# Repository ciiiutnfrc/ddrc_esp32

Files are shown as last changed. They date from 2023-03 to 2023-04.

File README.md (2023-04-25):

# DDRC-ESP32: Controlador para robot de tracción diferencial basado en ESP32

DDRC-ESP32 (Differential Driver Robot Controller con ESP32) es una placa de control embebido para robots de tracción diferencial. 
El controlador diferencial está basado en el módulo [ESP32-WROOM-32E](https://www.espressif.com/sites/default/files/documentation/esp32-wroom-32e_esp32-wroom-32ue_datasheet_en.pdf) de la marca [Espressif](https://www.espressif.com/), el cual cuenta con un SoC (System On Chip) modelo [ESP32-D0WD-V3](https://www.espressif.com/sites/default/files/documentation/esp32_datasheet_en.pdf).
La elección de este módulo se debe principalmente a que está soportado por [micro-ROS](https://micro.ros.org/docs/overview/hardware/). 

El desarrollo del controlador diferencial se llevó a cabo como Proyecto Final de la carrera de Ingeniería Electrónica en la [Facultad Regional Córdoba](https://www.frc.utn.edu.ar/) de la Universidad Tecnológica Nacional.
El título del proyecto es _"Controlador Embebido para Robot de Tracción Differencial"_ y fue desarrollado por Gustavo Albarrán, Dante Ruiz y Juan Nicolodi bajo la dirección del Ing. Gonzalo Perez-Paina y del Ing. Diego Gonzalez Dondo.

Este controlador tiene por finalidad servir de base al desarrollo de robots de tracción diferencial cuyos algoritmos de navegación y control estén basados en [ROS 2](http://docs.ros.org/).

Las funciones principales del controlador diferencial son:
1. Leer la información de los codificadores ópticos acoplados a las ruedas de tracción.
1. Ajustar las velocidades de los motores de tracción mediante controladores PID.
1. Realizar el cálculo de la odometrı́a con la información de los codificadores ópticos acoplados a las ruedas.
1. Leer la tensión de la(s) batería(s) del robot.
1. Comunicarse con la PC a bordo del robot.

La siguiente imagen muestra un render del PCB del controlador diferencial.
<p align="center">
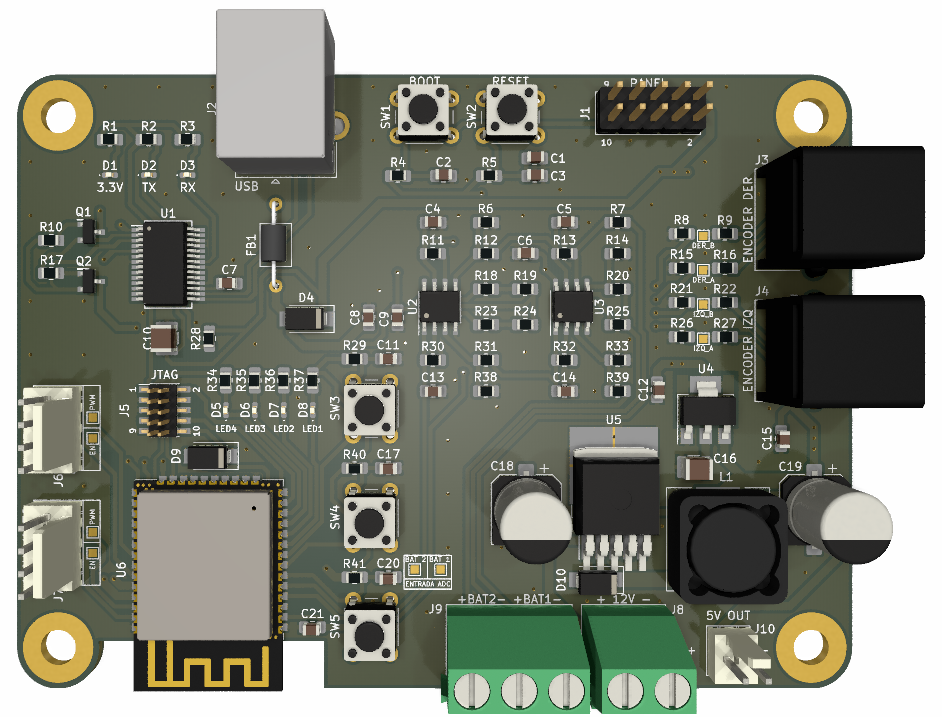
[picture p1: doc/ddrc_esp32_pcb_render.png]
DDRC-ESP32render
  
</p>

## Videos

* [Proyecto Final: Controlador para robot de tracción diferencial compatible con ROS 2](https://www.youtube.com/watch?v=9FsznQ60jsQ&ab_channel=CIIIUTN-FRC)

## Documentación adicional

* [Ejemplo `blink` con ESP-IDF y Docker](doc/IDFBlinkDocker.md)
* [Nodo micro-ROS de ejemplo en ESP32 con Docker](doc/ESP32MicroROS.md).
* [Servidor HTTP para evaluación sobre un robot móvil](doc/HTTPServerDDR.md).

## Licencia
  <p xmlns:cc="http://creativecommons.org/ns#" xmlns:dct="http://purl.org/dc/terms/"><a property="dct:title" rel="cc:attributionURL" href="https://github.com/ciiiutnfrc/ddrc_esp32">DDRC-ESP32: Controlador para robot de tracción diferencial basado en ESP32</a> by <span property="cc:attributionName">Gustavo Albarran, Dante Ruiz, Juan Nicolodi, Diego Gonzalez Dondo, Gonzalo Perez Paina</span> is licensed under <a href="http://creativecommons.org/licenses/by-sa/4.0/?ref=chooser-v1" target="_blank" rel="license noopener noreferrer" style="display:inline-block;">CC BY-SA 4.0</a></p>

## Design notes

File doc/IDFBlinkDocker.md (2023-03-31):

# Ejemplo `blink` con ESP-IDF y Docker

El framework de desarrollo oficial de Espressif se llama [ESP-IDF](https://docs.espressif.com/projects/esp-idf/en/latest/esp32/) (IoT Development Framework).
Para utilizar este framework es necesario instalar las siguientes herramientas:
1. El toolchain para compilar el código fuente del ESP32.
1. Las herramientas de construcción (como CMake y Ninja) para crear aplicaciones con el ESP32.
1. El propio ESP-IDF que contiene la API (bibliotecas de software y código fuente) para el ESP32 junto a varios scripts para operar con el toolchain.

Espressif brinda una [imagen Docker](https://docs.espressif.com/projects/esp-idf/en/latest/esp32/api-guides/tools/idf-docker-image.html) con el IDF listo para usar.
A continuación se muestran los pasos para instalar ESP-IDF usando Docker.

## Instalación de imagen Docker

La imagen se puede buscar con el siguiente comando:
```
> docker search espressif/idf
NAME                          DESCRIPTION                                     STARS     OFFICIAL   AUTOMATED
espressif/idf                 https://docs.espressif.com/projects/esp-idf/…   43                   
espressif/idf-rust-examples   Examples of rust on esp32                       2                    
espressif/idf-rust            ESP-IDF image with Rust support for Xtensa b…   7
```

Luego, la instalación de la imagen se realiza con:
```
> docker pull espressif/idf
```

La imágen instalada es:
```
 > docker images
espressif/idf                 latest             c82768a177c2   14 hours ago    4.16GB
```

El contenedor se puede ejecutar con el siguiente comando:
```
> docker run --rm -v $PWD:/home/esp-idf -w /home/esp-idf -it espressif/idf
```

El ESP-IDF incluye la herramienta de línea de comandos [`idf.py`](https://docs.espressif.com/projects/esp-idf/en/latest/esp32/api-guides/tools/idf-py.html) que sirve de front-end para administrar y construir los proyectos de forma simple. 
Se puede ver la instalada con:
```
> idf.py  --version

ESP-IDF v5.1-dev-3710-gacac972f70
```

## Ejemplo `blink`

Para la construcción y grabación del ejemplo `blink` primero ejecutar el contendor:
```
> docker run --rm --device=/dev/ttyUSB0:/dev/ttyUSB0 -it espressif/idf
```

El ejemplo `blink` se encuentra en `/opt/esp/idf/examples/get-started/blink/`.

Ir al directorio del ejemplo y seguir los siguientes pasos (basados en [enlace](https://github.com/espressif/esp-idf/tree/master/examples/get-started/blink)):
  1. Ingresar a la configuración del proyecto con `idf.py menuconfig`
  1. Ir a `Example Configuration`
  1. Modificar el GPIO del LED (en el controlador diferencial el `LED1` se encuentra en el `GPIO33`)
  1. Salir y guardar los cambios
  1. Construir con `idf.py build`
  1. Grabar con `idf.py -p /dev/ttyUSB0 flash`

El `LED1` de la placa comienza a parpadear cada 1 seg.

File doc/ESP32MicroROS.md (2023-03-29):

# Nodo micro-ROS ejemplo en ESP32 con Docker

Se muestran los pasos a seguir para construir y grabar en la placa un nodo ejemplo de micro-ROS utilizando Docker.

La información de esta página se obtuvo de los siguientes enlaces:
* [micro-ROS setup (github)](https://github.com/micro-ROS/micro_ros_setup)
* [micro-ROS porting to ESP32](https://micro.ros.org/blog/2020/08/27/esp32/)

## ROS 2 en Docker

Ejecutar un contenedor Docker a partir de la imagen de ROS 2 (`ros:galactic-desktop`):
```
> mkdir $HOME/ros2_ws && cd $HOME/ros2_ws
> docker run -it -v $PWD:/home/ros2_ws -w /home/ros2_ws --net=host --privileged --name micro_ros_esp32 --device=/dev/ttyUSB0:/dev/ttyUSB0 osrf/ros:galactic-desktop
```

Actualizar el SO e instalar PIP:
```
> apt update
> apt install vim python3-pip
```

## micro-ROS para ESP32
Crear el espacio de trabajo para ROS 2 con soporta al ESP32, instalar las dependencias y construirlo:
```
> git clone -b $ROS_DISTRO https://github.com/micro-ROS/micro_ros_setup.git src/micro_ros_setup
> rosdep update && rosdep install --from-paths src --ignore-src -y
> colcon build
> source install/local_setup.bash
```

Crear el entorno de trabajo para el firmware del ESP32:
```
> ros2 run micro_ros_setup create_firmware_ws.sh freertos esp32
```

Configurar el proyecto del ESP32 a utilizar:
```
> ros2 run micro_ros_setup configure_firmware.sh int32_publisher -t udp -i [your local machine IP] -p 8888
> ros2 run micro_ros_setup build_firmware.sh menuconfig
```

Utilizar el menú para configuración del proyecto para configurar la conexión WiFi. 
Ir a la opción `micro-ROS Transport Settings` luego `WiFi Connection` y escribir el nombre (`WiFi SSID`) y la clave (`WiFi Password`) de la conexión de red a utilizar.

Construir el proyecto:
```
> ros2 run micro_ros_setup build_firmware.sh
```

Descargar el programa en el microcontrolador:
```
> ros2 run micro_ros_setup flash_firmware.sh
```

## Ejecución del agente y prueba del nodo

Descargar, construir y ejecutar el agente:
```
> ros2 run micro_ros_setup create_agent_ws.sh
> ros2 run micro_ros_setup build_agent.sh
> source install/local_setup.bash
> ros2 run micro_ros_agent micro_ros_agent udp4 --port 8888
```

Abrir otra terminal del contenedor en ejecución:
```
> docker exec -it micro_ros_esp32 bash
```

y ver la información de nodos y tópicos:
```
> source /opt/ros/galactic/setup.bash
> ros2 node list
/freertos_int32_publisher

> ros2 topic list
/freertos_int32_publisher
/parameter_events
/rosout
```

Mostrar el mensaje enviado por el ESP32:
```
> ros2 topic echo /freertos_int32_publisher
data: 4
- - -
data: 5
- - -
data: 6
```

### Agente desde Docker

También se puede utilizar el agente en un contenedor Docker:
```
> docker run -it --rm --net=host microros/micro-ros-agent:galactic udp4 --port 8888 -v6
```

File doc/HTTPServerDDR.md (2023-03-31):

# Servidor HTTP para evaluación sobre un robot móvil

Esta aplicación sirve para evaluar las funcionalidades del controlador montado sobre un robot de traccióń diferencial. Fue evaluado sobre el Robot móvil [RoMAA-II](https://ciii.frc.utn.edu.ar/wiki/Robotica/RoMAARobot).

Para grabar la aplicación en el controlador se debe clonar el presente repositorio y desde la shell de Linux ir al subdirectorio `src/http_server/`. Una vez en este directorio y con el controlador conectado a la PC, ejecutar:
```
> docker run --rm --device=/dev/ttyUSB0:/dev/ttyUSB0 -v $PWD:/home/http_server -w /home/http_server -it espressif/idf
```

Construir y grabar la aplicación con:
```
> idf.py build
> idf.py flash
```

La aplicación generar una red WiFi con los siguientes datos:
* SSID: ddrc
* Pass: ddrc1234

Una vez conectado a esta red, utilizar un navegador para ingresar a la dirección 192.168.4.1.

Los parámetros de la red (SSID y Pass) se puede modificar utilizando el comando `idf.py menuconfig`.

Para depurar el comportamiento de la aplicación se puede utilizar el monitor del ESP32 con:
```
> idf.py monitor
```

Para salir del monitor utilizar la combinación de teclas `Ctrl+]`.

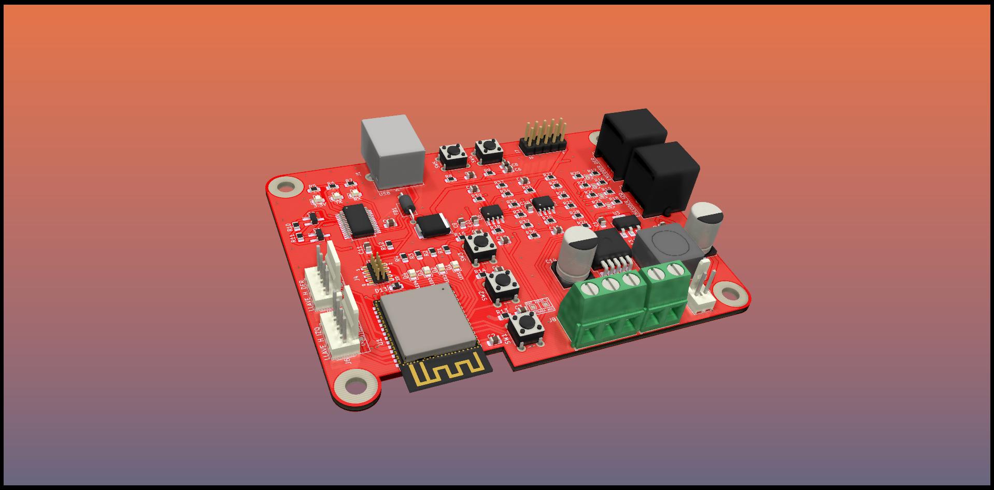
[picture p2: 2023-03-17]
hardware/main_board/imagen_esp_controller_PCB.jpg

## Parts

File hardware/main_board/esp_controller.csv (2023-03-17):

Id | Identificador | Empaquetado | Cantidad | Identificación | Suministrador y ref
1 | TP10,TP8,TP9,TP7,TP6,TP4,TP3,TP5,TP2,TP1 | TestPoint_Pad_1.0x1.0mm | 10 | TP
2 | C21,C20,C19,C18,C17,C16,C12,C10,C8,C7,C6,C5,C4,C3,C2 | C_0805_2012Metric_Pad1.18x1.45mm_HandSolder | 15 | 100nF
3 | U1 | ESP32-WROOM-32E-with-keep-area | 1 | ESP32-WROOM-32E
4 | J10 | Molex_KK-254_AE-6410-02A_1x02_P2.54mm_Vertical | 1 | Conn_01x02
5 | J9 | TerminalBlock_Phoenix_MKDS-1,5-2-5.08_1x02_P5.08mm_Horizontal | 1 | Conn_01x02
6 | D8 | D_SMA_Handsoldering | 1 | 1N5824
7 | J1 | USB_B_OST_USB-B1HSxx_Horizontal | 1 | USB_B
8 | J3,J2 | RJ14_Connfly_DS1133-S4_Horizontal | 2 | RJ14
9 | U6,U5 | SOIC-8_3.9x4.9mm_P1.27mm | 2 | MCP6002-xSN
10 | U4 | TO-263-5_TabPin3 | 1 | LM2596S-5
11 | R39,R38,R12 | R_0805_2012Metric_Pad1.20x1.40mm_HandSolder | 3 | 1k
12 | R37,R36,R27,R26,R25,R24,R23,R22,R21,R20,R15,R14,R13,R11,R10,R9,R8 | R_0805_2012Metric_Pad1.20x1.40mm_HandSolder | 17 | 10k
13 | R35,R33 | R_0805_2012Metric_Pad1.20x1.40mm_HandSolder | 2 | 2.5k
14 | R34,R32 | R_0805_2012Metric_Pad1.20x1.40mm_HandSolder | 2 | 2k
15 | R31,R30,R29,R28 | R_0805_2012Metric_Pad1.20x1.40mm_HandSolder | 4 | 2.2k
16 | R19,R18,R17,R16 | R_0805_2012Metric_Pad1.20x1.40mm_HandSolder | 4 | 27k
17 | R7,R6,R5,R4,R3,R2,R1 | R_0805_2012Metric_Pad1.20x1.40mm_HandSolder | 7 | 270
18 | L1 | L_12x12mm_H8mm | 1 | 33uH
19 | D13 | D_0805_2012Metric_Pad1.15x1.40mm_HandSolder | 1 | D
20 | D12 | D_2816_7142Metric_Pad3.20x4.45mm_HandSolder | 1 | SS34
21 | D7,D6,D5,D4,D3,D2,D1 | LED_0805_2012Metric_Pad1.15x1.40mm_HandSolder | 7 | LED
22 | C15,C14 | CP_Elec_8x11.9 | 2 | 680uF
23 | C13,C1 | C_0805_2012Metric_Pad1.18x1.45mm_HandSolder | 2 | 22uF
24 | C11 | C_0805_2012Metric_Pad1.18x1.45mm_HandSolder | 1 | 4.7uF
25 | C9 | C_0805_2012Metric_Pad1.18x1.45mm_HandSolder | 1 | 10nF
26 | Q2,Q1 | SOT-23_Handsoldering | 2 | S8050
27 | U3 | SOT-223-3_TabPin2 | 1 | AMS1117-3.3
28 | J8 | TerminalBlock_Phoenix_MKDS-1,5-3-5.08_1x03_P5.08mm_Horizontal | 1 | Conn_01x03
29 | J7 | PinHeader_2x05_P2.54mm_Vertical | 1 | Conn_02x05_Odd_Even
30 | J6,J5 | Molex_KK-254_AE-6410-04A_1x04_P2.54mm_Vertical | 2 | Conn_01x04
31 | J4 | PinHeader_2x05_P1.27mm_Vertical_SMD | 1 | Conn_02x05_Odd_Even
32 | SW5,SW4,SW3,SW2,SW1 | SW_PUSH_6mm | 5 | SW_Push
33 | FB1 | L_Axial_L5.0mm_D3.6mm_P10.00mm_Horizontal_Murata_BL01RN1A2A2 | 1 | Ferrite_Bead
34 | U2 | SSOP-28_5.3x10.2mm_P0.65mm | 1 | FT232RL
35 | H4,H3,H2,H1 | MountingHole_4.3mm_M4_Pad | 4 | MountingHole_4.3mm_M4_Pad

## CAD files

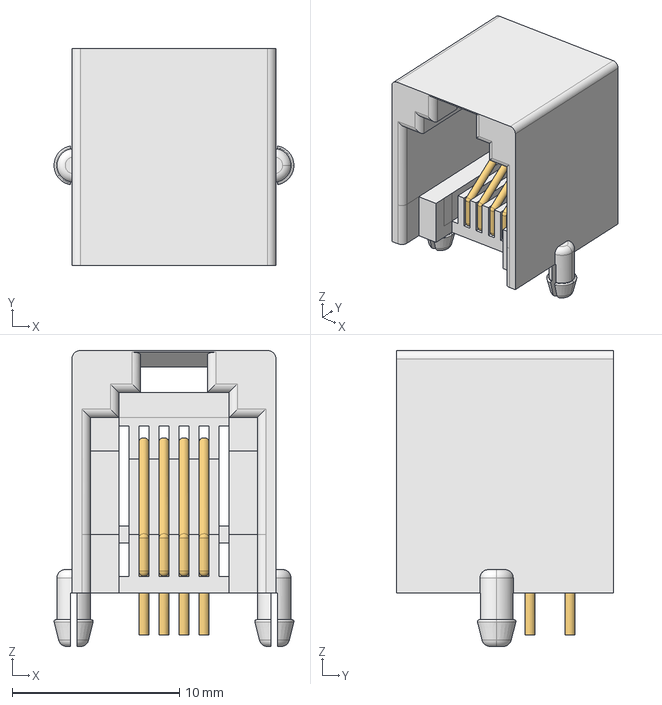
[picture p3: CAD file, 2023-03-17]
hardware/kicad_lib/3d/RJ11.step
14.3 x 13.0 x 17.7 mm

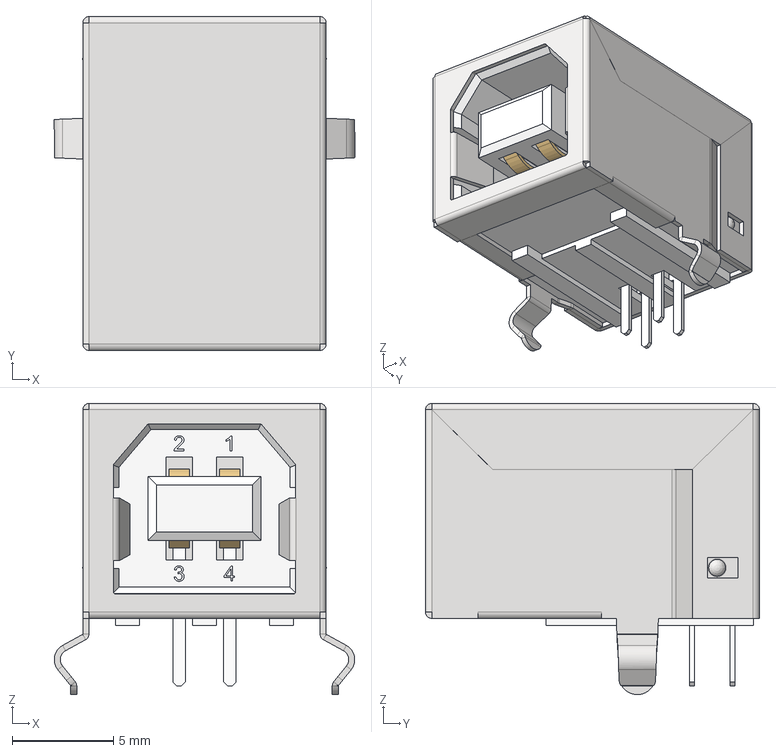
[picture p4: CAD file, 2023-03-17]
hardware/kicad_lib/3d/USB 2.0 Type B Connector Right Angle (Würth 61400416121).stp
14.8 x 16.5 x 14.4 mm

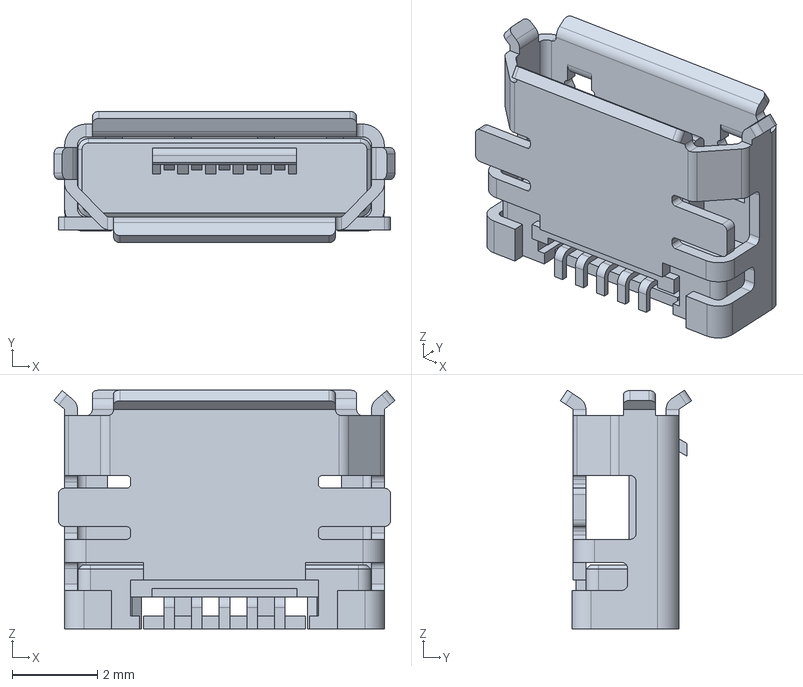
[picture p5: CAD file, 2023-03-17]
hardware/kicad_lib/3d/USB-B-micro.stp
8.00 x 3.08 x 5.60 mm

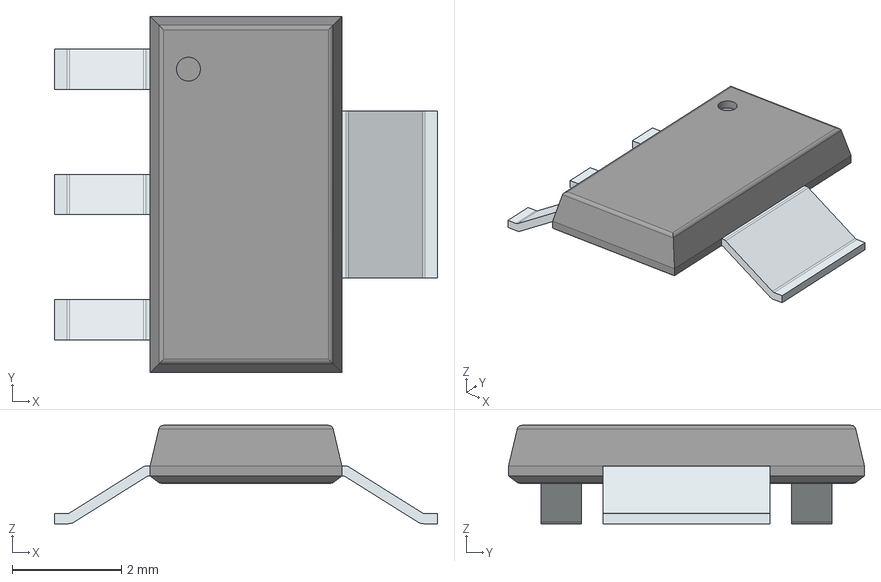
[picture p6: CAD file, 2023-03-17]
hardware/kicad_lib/3d/AMS1117-3.3.stp
7.00 x 6.50 x 1.80 mm
PinsArrayL
FilletPinR

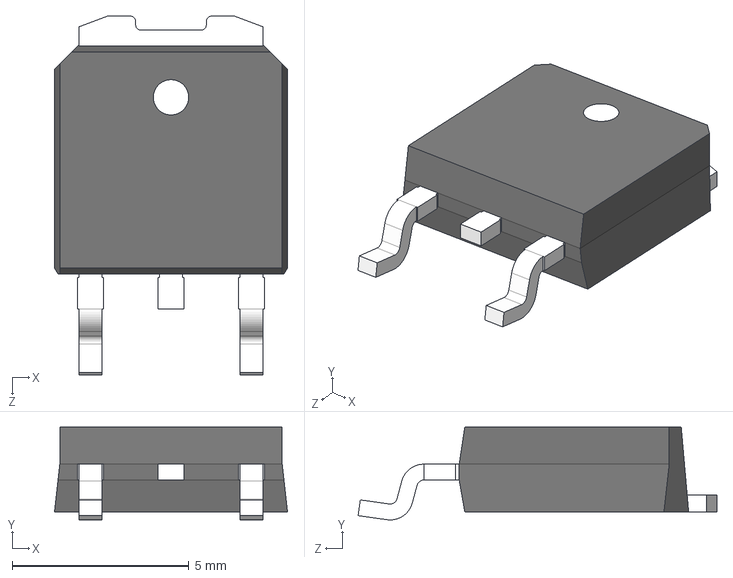
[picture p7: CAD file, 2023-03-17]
hardware/kicad_lib/3d/L7805CDT-TR.stp
6.60 x 2.63 x 10.2 mm

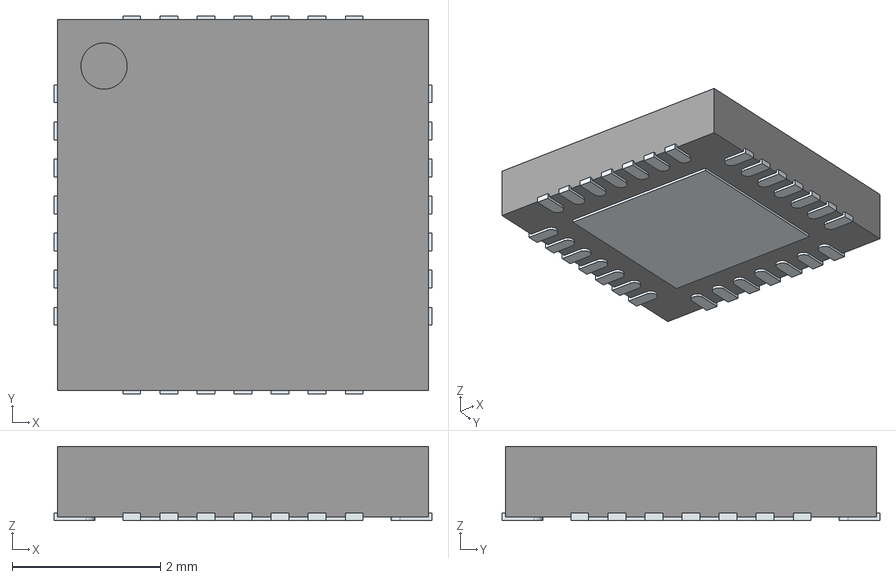
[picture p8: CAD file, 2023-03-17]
hardware/kicad_lib/3d/CP2102-GMR.stp
5.10 x 5.10 x 1.00 mm
ThermalPin
PinsArrayLR
PinsArrayTB

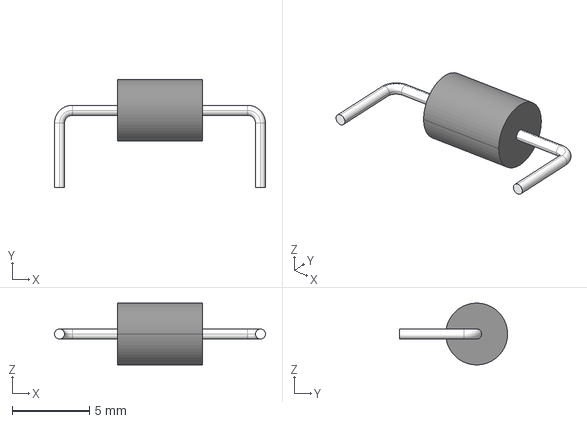
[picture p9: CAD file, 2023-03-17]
hardware/kicad_lib/3d/ferrite-h_p13_d4_l5-5.stp
13.6 x 7.00 x 4.00 mm

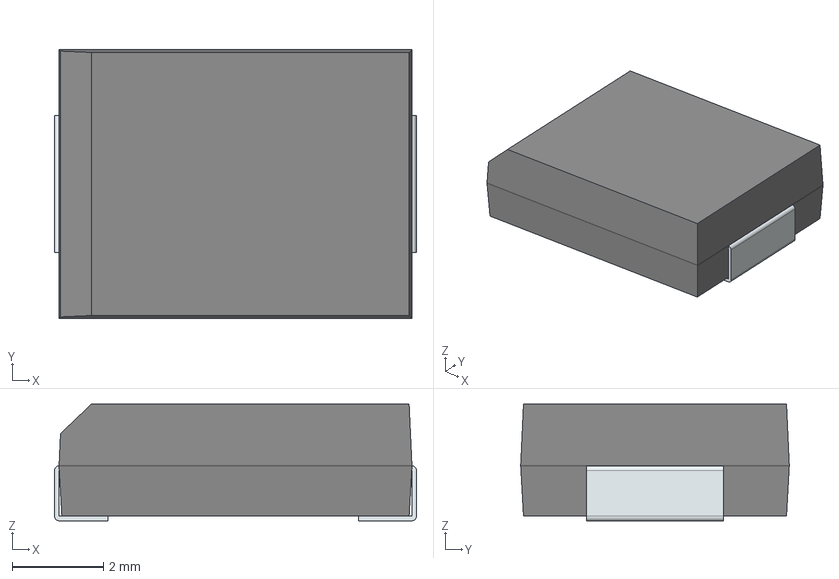
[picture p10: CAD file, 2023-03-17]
hardware/kicad_lib/3d/SS34.stp
7.95 x 5.90 x 2.56 mm
FilletPin1
FilletPin2

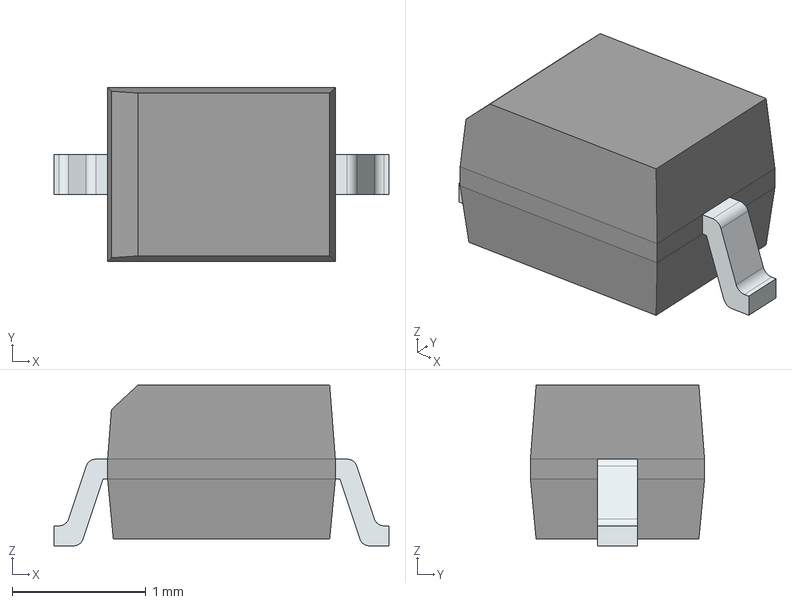
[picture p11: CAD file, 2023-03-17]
hardware/kicad_lib/3d/BAT760-7.stp
2.50 x 1.30 x 1.20 mm
FilletPinL
FilletPinR

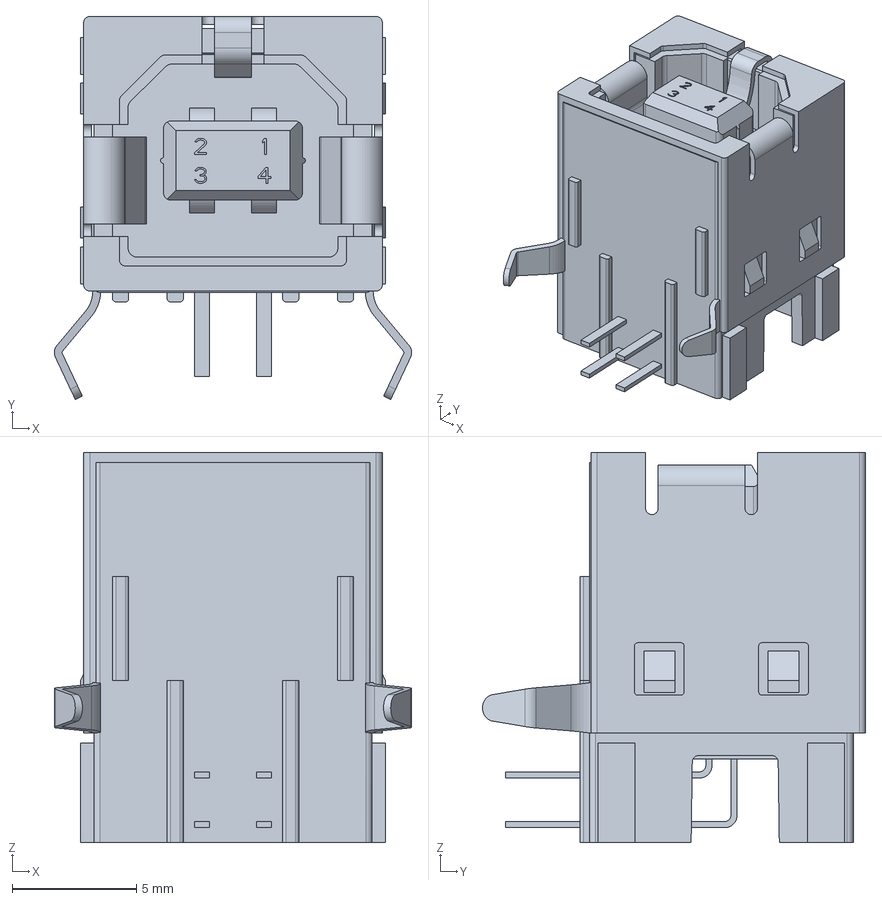
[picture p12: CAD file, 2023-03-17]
hardware/kicad_lib/3d/USB-B.stp
14.4 x 15.4 x 15.7 mm

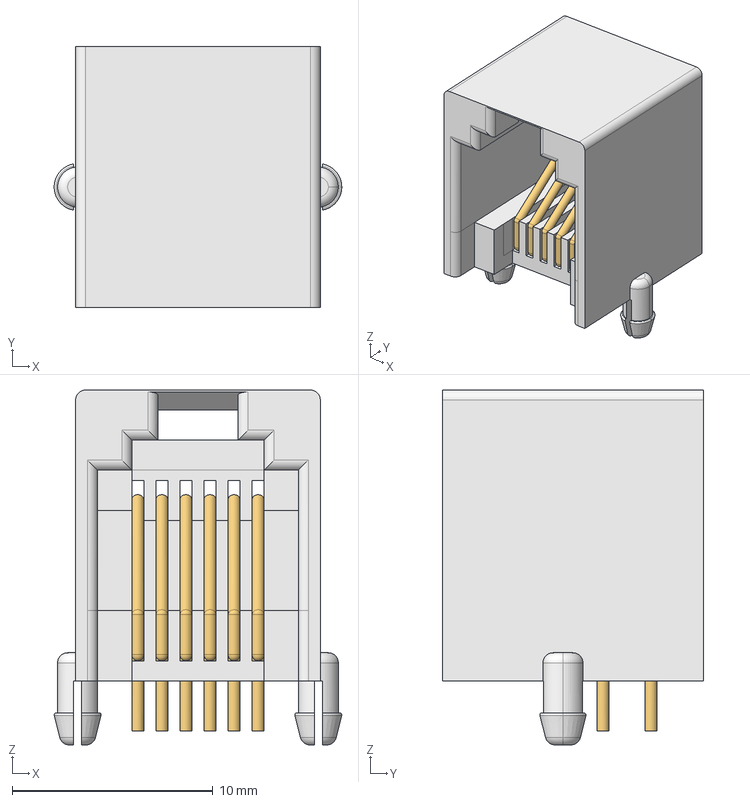
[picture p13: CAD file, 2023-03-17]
hardware/kicad_lib/3d/RJ12.step
14.3 x 13.0 x 17.7 mm

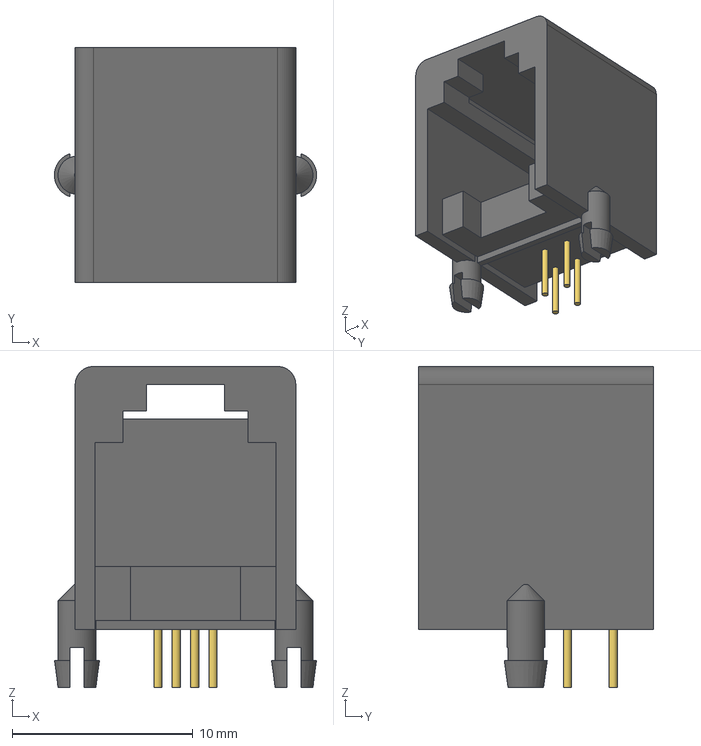
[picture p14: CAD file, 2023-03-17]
hardware/kicad_lib/3d/TJ6P4C.stp
14.5 x 13.0 x 17.8 mm

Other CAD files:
hardware/kicad_lib/3d/BAT760-7.stl
hardware/kicad_lib/3d/SS34.stl

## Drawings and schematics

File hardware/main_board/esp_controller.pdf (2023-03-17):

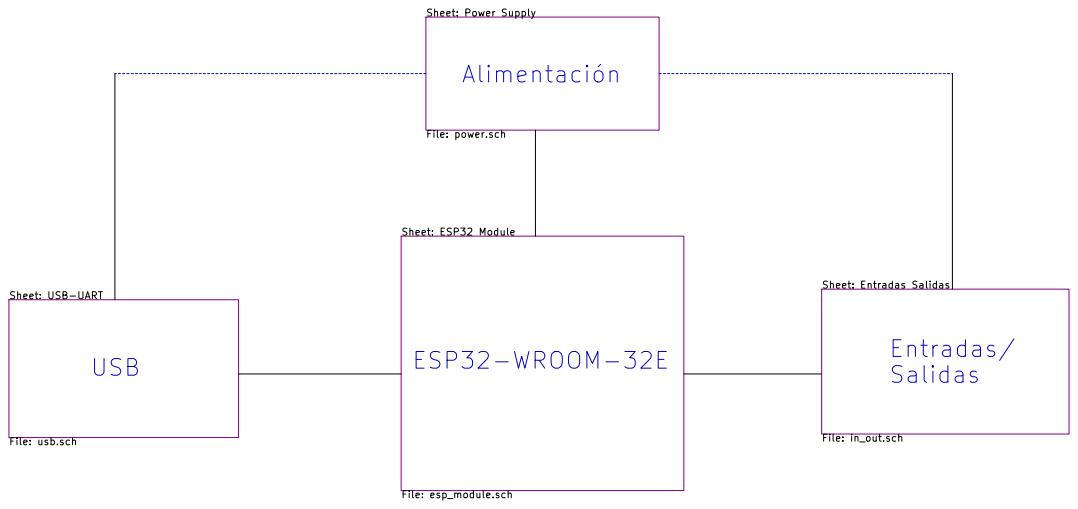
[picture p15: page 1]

Sheet: ESP32 Module File: esp_module.sch Sheet: USB-UART

File: esp_controller.sch Sheet: /
Id: 1/5 Title: Controlador embebido para robot de tracción diferencial

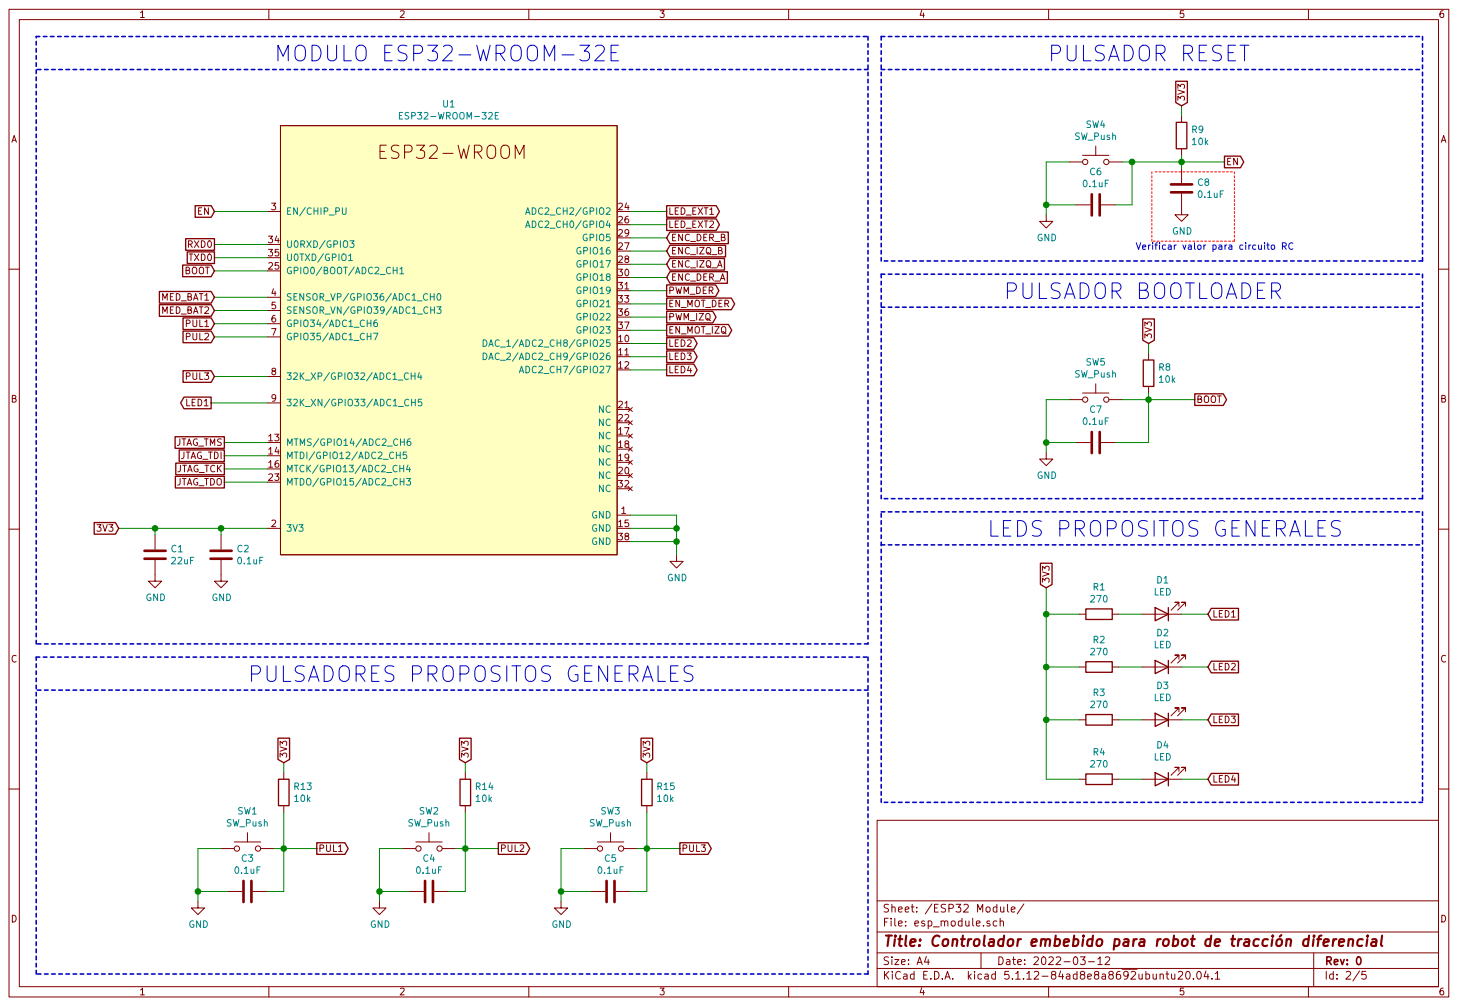
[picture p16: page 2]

Verificar valor para circuito RC

Id: 2/5 Title: Controlador embebido para robot de tracción diferencial

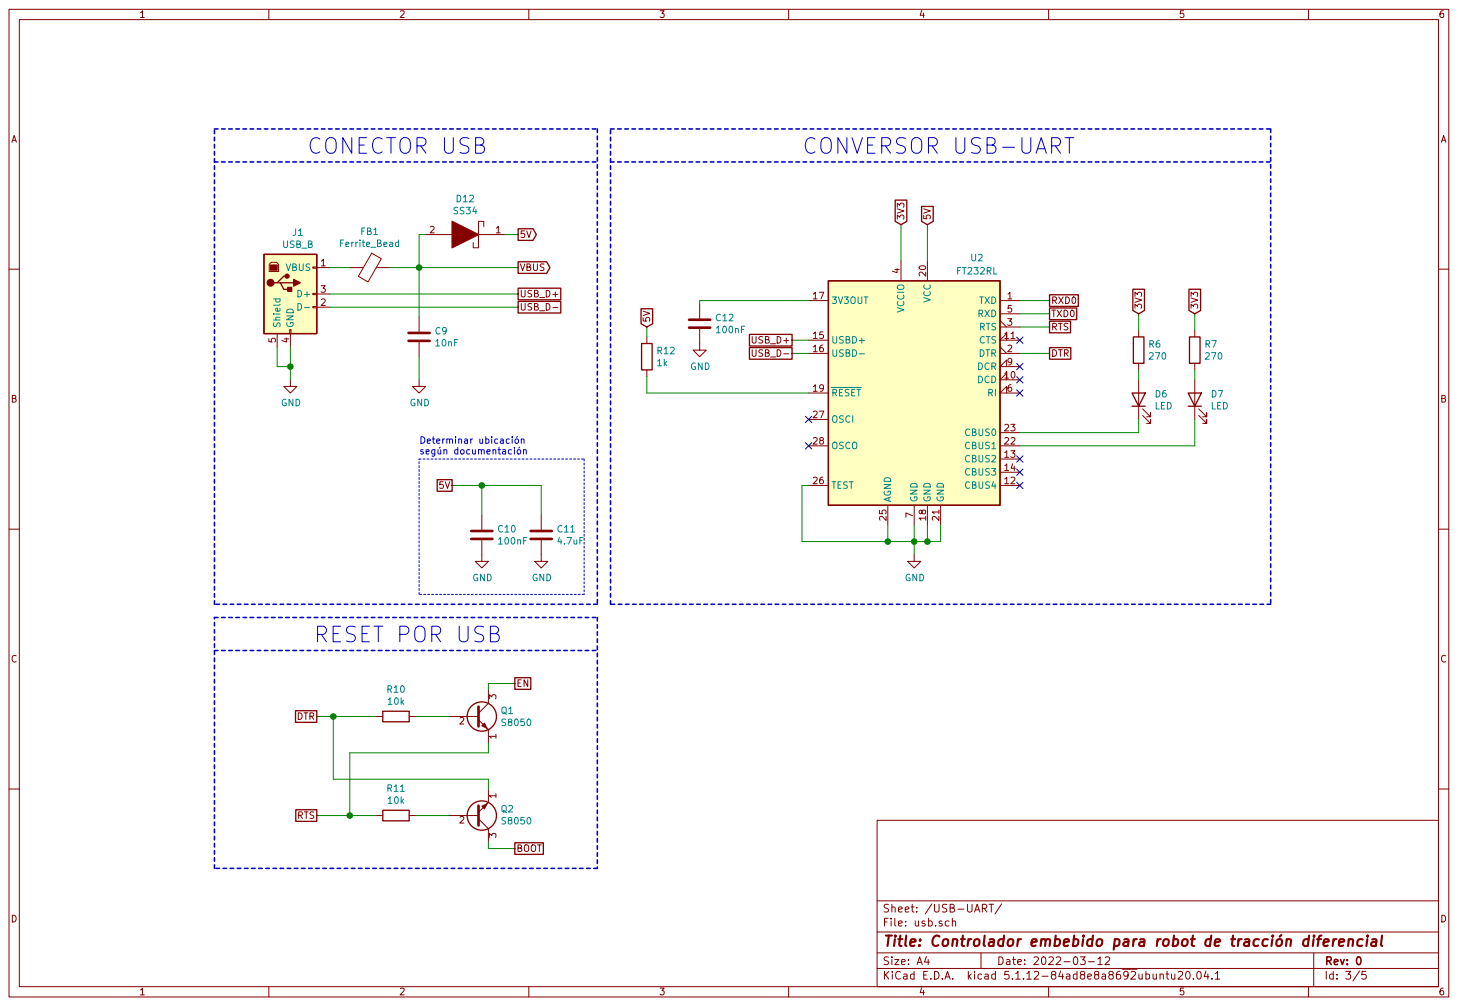
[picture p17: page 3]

Id: 3/5 Title: Controlador embebido para robot de tracción diferencial File: usb.sch Sheet: /USB-UART/ C11

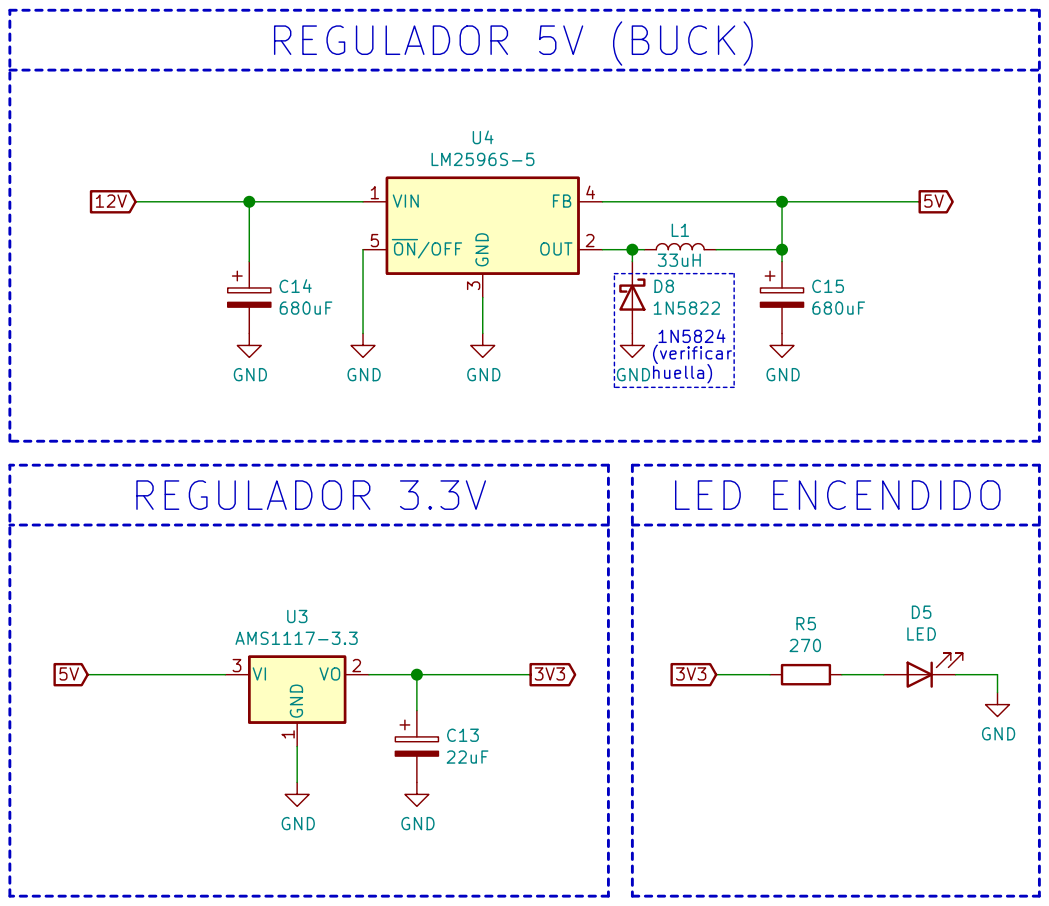
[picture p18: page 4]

File: power.sch
Id: 4/5 Title: Controlador embebido para robot de tracción diferencial

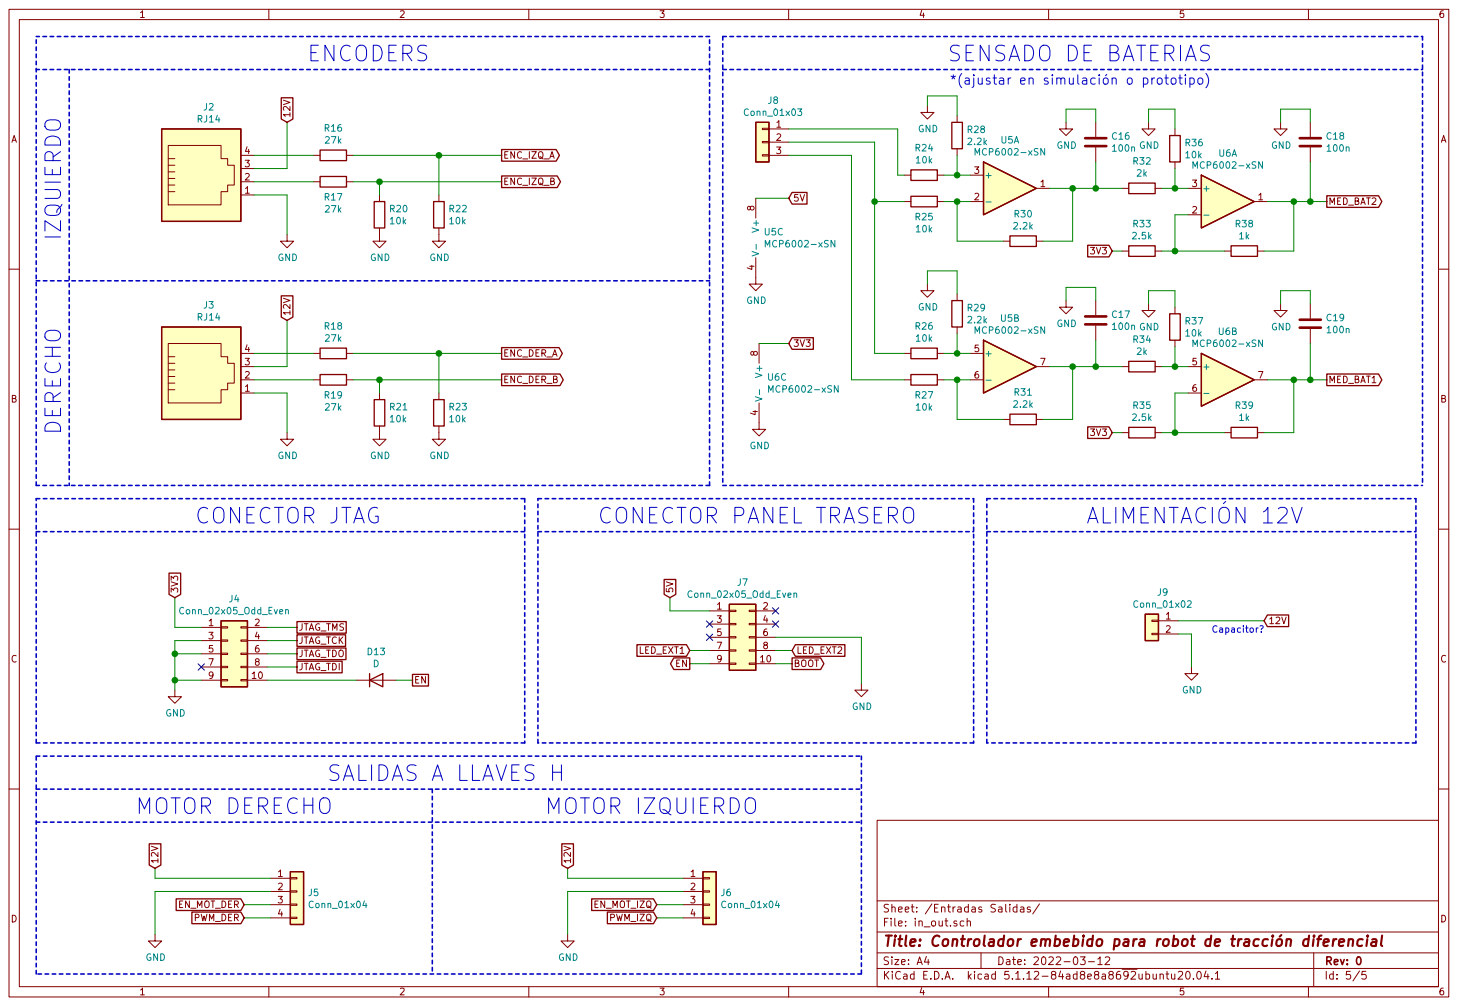
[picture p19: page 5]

*(ajustar en simulación o prototipo) IZQUIERDO

ENC_IZQ_B 12V

10k GND

Id: 5/5 Title: Controlador embebido para robot de tracción diferencial

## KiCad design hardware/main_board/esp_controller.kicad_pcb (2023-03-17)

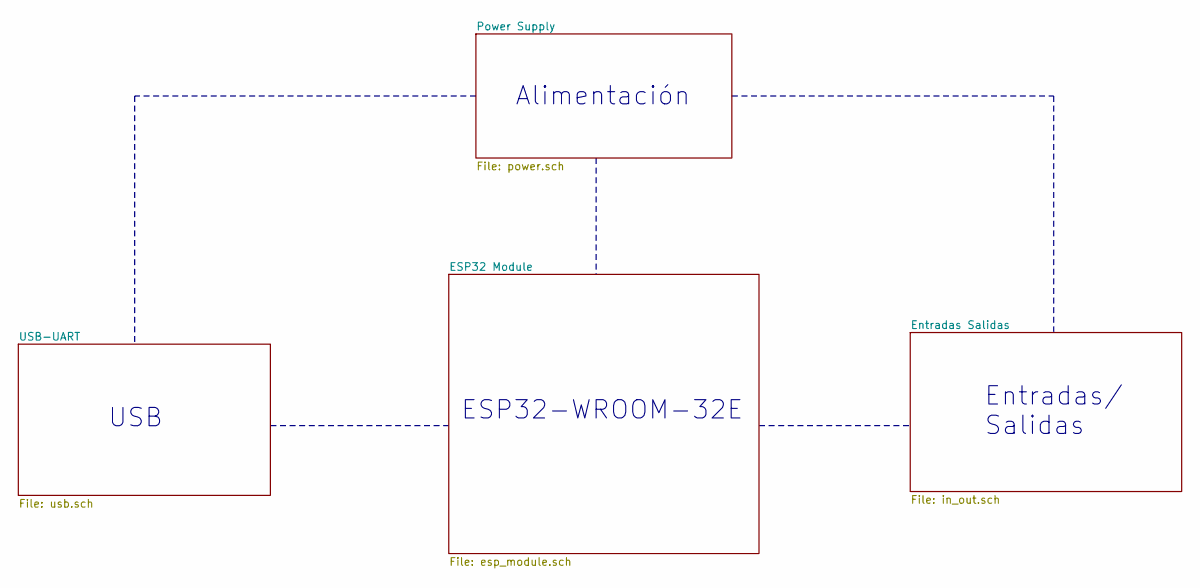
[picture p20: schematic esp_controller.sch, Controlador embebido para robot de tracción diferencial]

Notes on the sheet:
Alimentación
Entradas/ Salidas
USB
ESP32-WROOM-32E

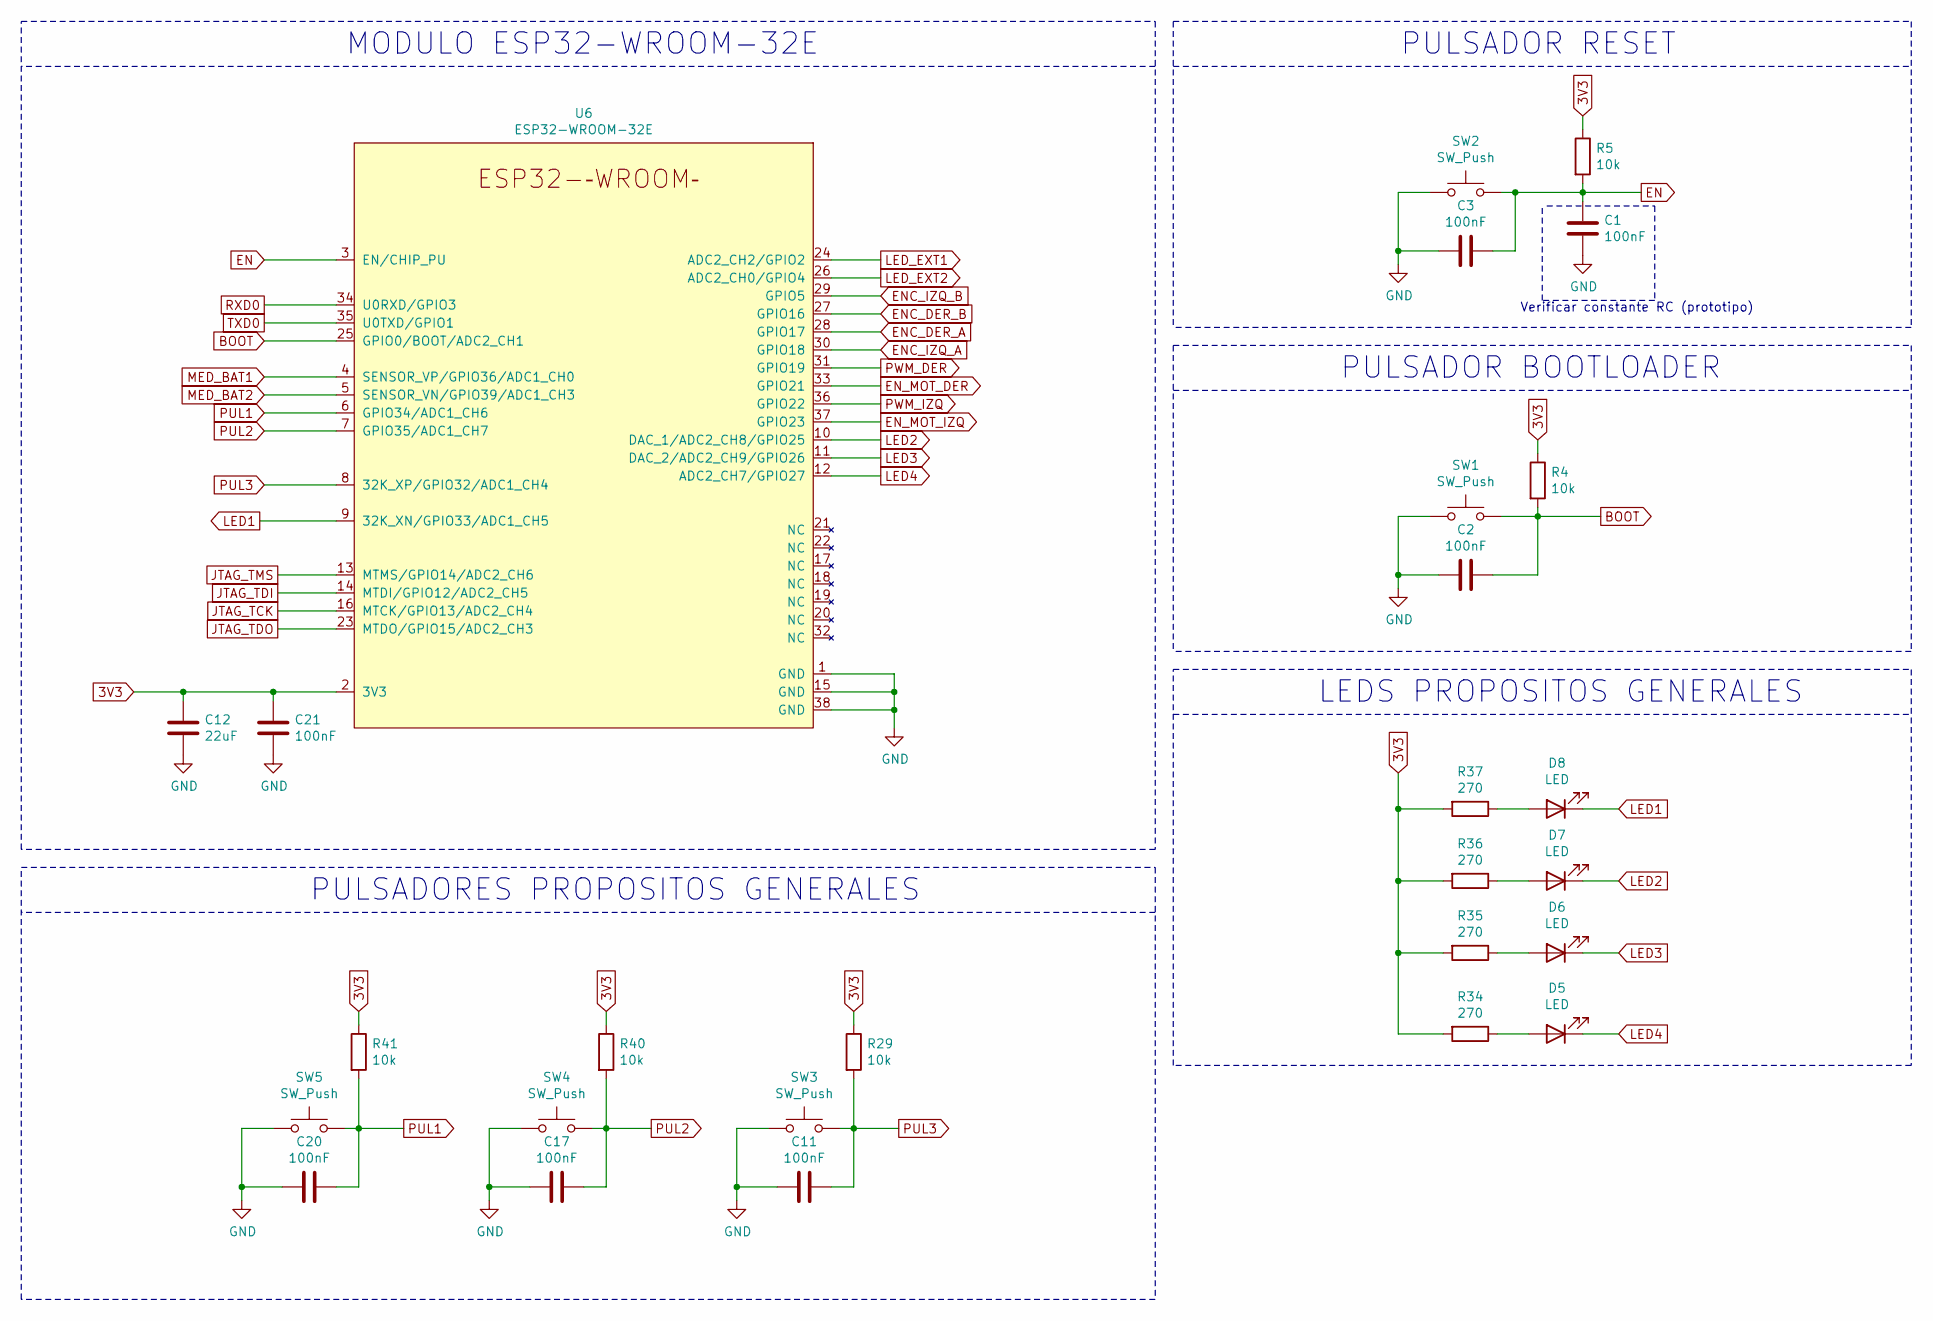
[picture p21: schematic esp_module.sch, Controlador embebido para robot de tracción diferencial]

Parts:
C1, C2, C3, C11, C17, C20, C21: 100nF; C_0805_2012Metric_Pad1.18x1.45mm_HandSolder
C12: 22uF; C_0805_2012Metric_Pad1.18x1.45mm_HandSolder
D5, D6, D7, D8: LED; LED_0402_1005Metric_Pad0.77x0.64mm_HandSolder
R4, R5, R29, R40, R41: 10k; R_0805_2012Metric_Pad1.20x1.40mm_HandSolder
R34, R35, R36, R37: 270; R_0805_2012Metric_Pad1.20x1.40mm_HandSolder
SW1, SW2, SW3, SW4, SW5: SW_Push; SW_PUSH_6mm
U6: ESP32-WROOM-32E; ESP32-WROOM-32E-with-keep-area

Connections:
3V3: C12.1, C21.1, R4.1, R5.1, R29.1, R34.2, R35.2, R36.2, R37.2, R40.1, R41.1, U6.2 (3V3); also elsewhere on the board
BOOT: C2.1, R4.2, SW1.2, U6.25 (GPIO0/BOOT/ADC2_CH1); also elsewhere on the board
EN: C1.1, C3.1, R5.2, SW2.2, U6.3 (EN/CHIP_PU); also elsewhere on the board
ENC_DER_A: U6.28 (GPIO17); also elsewhere on the board
ENC_DER_B: U6.27 (GPIO16); also elsewhere on the board
ENC_IZQ_A: U6.30 (GPIO18); also elsewhere on the board
ENC_IZQ_B: U6.29 (GPIO5); also elsewhere on the board
EN_MOT_DER: U6.33 (GPIO21); also elsewhere on the board
EN_MOT_IZQ: U6.37 (GPIO23); also elsewhere on the board
GND: C1.2, C2.2, C3.2, C11.2, C12.2, C17.2, C20.2, C21.2, SW1.1, SW2.1, SW3.1, SW4.1, SW5.1, U6.1 (GND), U6.15 (GND), U6.38 (GND); also elsewhere on the board
JTAG_TCK: U6.16 (MTCK/GPIO13/ADC2_CH4); also elsewhere on the board
JTAG_TDI: U6.14 (MTDI/GPIO12/ADC2_CH5); also elsewhere on the board
JTAG_TDO: U6.23 (MTDO/GPIO15/ADC2_CH3); also elsewhere on the board
JTAG_TMS: U6.13 (MTMS/GPIO14/ADC2_CH6); also elsewhere on the board
LED1: D8.1 (K), U6.9 (32K_XN/GPIO33/ADC1_CH5)
LED2: D7.1 (K), U6.10 (DAC_1/ADC2_CH8/GPIO25)
LED3: D6.1 (K), U6.11 (DAC_2/ADC2_CH9/GPIO26)
LED4: D5.1 (K), U6.12 (ADC2_CH7/GPIO27)
LED_EXT1: U6.24 (ADC2_CH2/GPIO2); also elsewhere on the board
LED_EXT2: U6.26 (ADC2_CH0/GPIO4); also elsewhere on the board
MED_BAT1: U6.4 (SENSOR_VP/GPIO36/ADC1_CH0); also elsewhere on the board
MED_BAT2: U6.5 (SENSOR_VN/GPIO39/ADC1_CH3); also elsewhere on the board
unnamed: D5.2 (A), R34.1
unnamed: D6.2 (A), R35.1
unnamed: D7.2 (A), R36.1
unnamed: D8.2 (A), R37.1
PUL1: C20.1, R41.2, SW5.2, U6.6 (GPIO34/ADC1_CH6)
PUL2: C17.1, R40.2, SW4.2, U6.7 (GPIO35/ADC1_CH7)
PUL3: C11.1, R29.2, SW3.2, U6.8 (32K_XP/GPIO32/ADC1_CH4)
PWM_DER: U6.31 (GPIO19); also elsewhere on the board
PWM_IZQ: U6.36 (GPIO22); also elsewhere on the board
RXD0: U6.34 (U0RXD/GPIO3); also elsewhere on the board
TXD0: U6.35 (U0TXD/GPIO1); also elsewhere on the board

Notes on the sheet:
PULSADOR RESET
PULSADOR BOOTLOADER
LEDS PROPOSITOS GENERALES
PULSADORES PROPOSITOS GENERALES
MODULO ESP32-WROOM-32E
Verificar constante RC (prototipo)

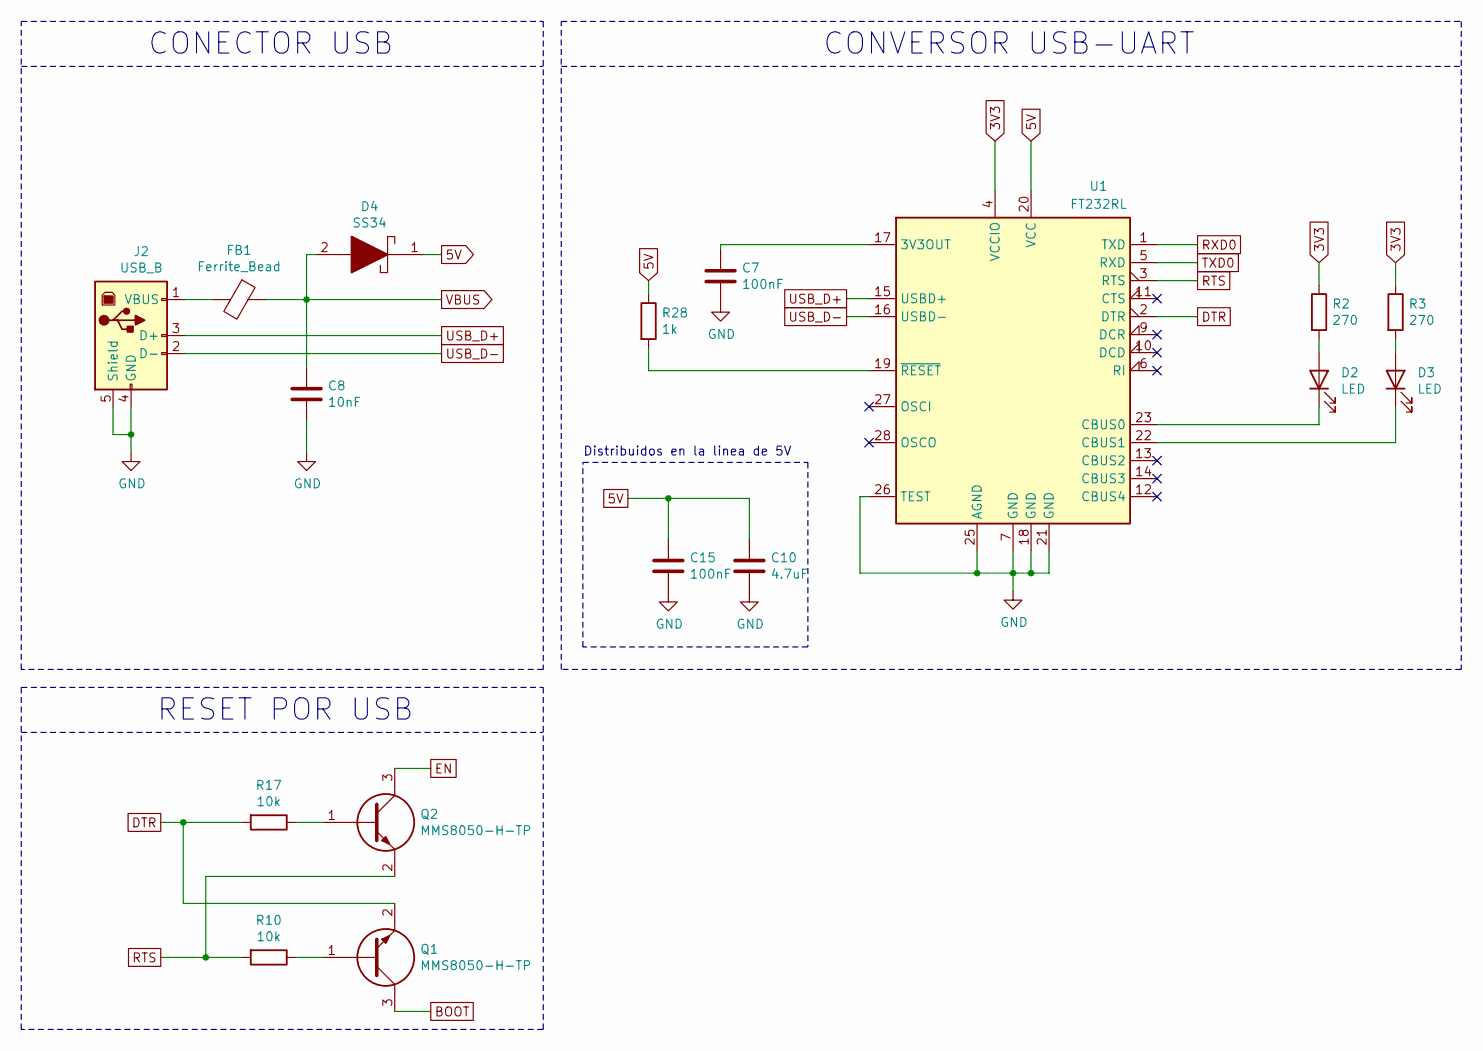
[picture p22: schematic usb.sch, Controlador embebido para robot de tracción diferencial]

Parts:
C7, C15: 100nF; C_0805_2012Metric_Pad1.18x1.45mm_HandSolder
C8: 10nF; C_0805_2012Metric_Pad1.18x1.45mm_HandSolder
C10: 4.7uF; C_1210_3225Metric
D2, D3: LED; LED_0402_1005Metric_Pad0.77x0.64mm_HandSolder
D4: SS34; D_SMA; Manufacturer_Part_Number SS34; Mouser Part Number 512-SS34
FB1: Ferrite_Bead; L_Axial_L5.0mm_D3.6mm_P10.00mm_Horizontal_Murata_BL01RN1A2A2
J2: USB_B; USB_B_OST_USB-B1HSxx_Horizontal
Q1, Q2: MMS8050-H-TP; SOT96P237X122-3N; Manufacturer_Part_Number MMS8050-H-TP; Mouser Part Number 833-MMS8050-H-TP
R2, R3: 270; R_0805_2012Metric_Pad1.20x1.40mm_HandSolder
R10, R17: 10k; R_0805_2012Metric_Pad1.20x1.40mm_HandSolder
R28: 1k; R_0805_2012Metric_Pad1.20x1.40mm_HandSolder
U1: FT232RL; SSOP-28_5.3x10.2mm_P0.65mm

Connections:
3V3: R2.1, R3.1, U1.4 (VCCIO); also elsewhere on the board
5V: C10.1, C15.1, D4.1, R28.1, U1.20 (VCC); also elsewhere on the board
BOOT: Q1.3; also elsewhere on the board
DTR: Q1.2, R17.2, U1.2 (DTR)
EN: Q2.3; also elsewhere on the board
GND: C7.2, C8.2, C10.2, C15.2, J2.4 (GND), J2.5 (Shield), U1.7 (GND), U1.18 (GND), U1.21 (GND), U1.25 (AGND), U1.26 (TEST); also elsewhere on the board
unnamed: C7.1, U1.17 (3V3OUT)
unnamed: D2.1 (K), U1.23 (CBUS0)
unnamed: D2.2 (A), R2.2
unnamed: D3.1 (K), U1.22 (CBUS1)
unnamed: D3.2 (A), R3.2
unnamed: FB1.2, J2.1 (VBUS)
unnamed: Q1.1, R10.1
unnamed: Q2.1, R17.1
unnamed: R28.2, U1.19 (~RESET~)
RTS: Q2.2, R10.2, U1.3 (RTS)
RXD0: U1.1 (TXD); also elsewhere on the board
TXD0: U1.5 (RXD); also elsewhere on the board
USB_D+: J2.3 (D+), U1.15 (USBD+)
USB_D-: J2.2 (D-), U1.16 (USBD-)
VBUS: C8.1, D4.2, FB1.1

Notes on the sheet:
Distribuidos en la linea de 5V
CONECTOR USB
CONVERSOR USB-UART
RESET POR USB

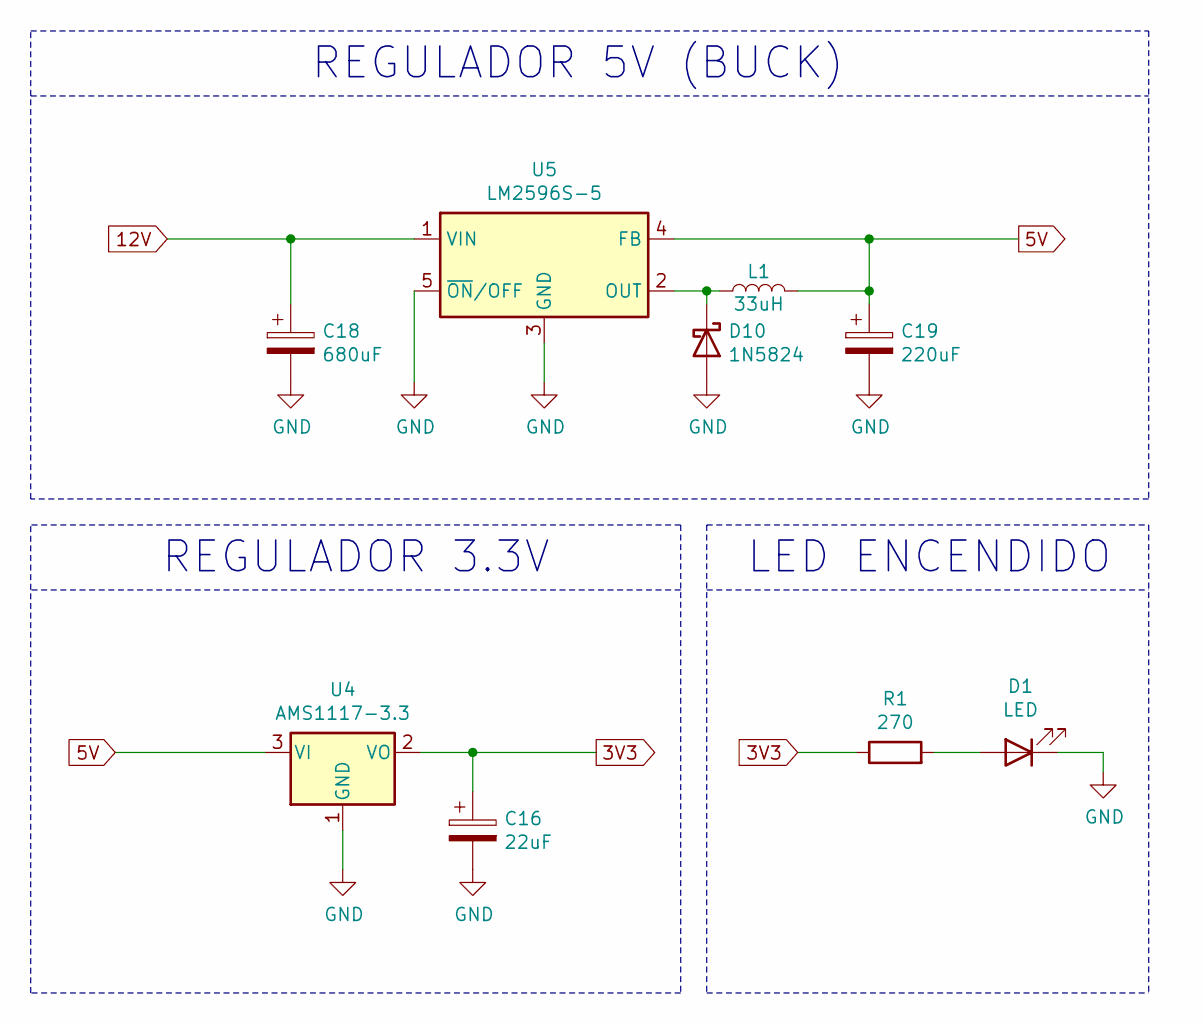
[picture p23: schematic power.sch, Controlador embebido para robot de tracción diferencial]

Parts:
C16: 22uF; C_1210_3225Metric
C18: 680uF; CP_Elec_8x11.9
C19: 220uF; CP_Elec_8x11.9
D1: LED; LED_0402_1005Metric_Pad0.77x0.64mm_HandSolder
D10: 1N5824; D_SMA
L1: 33uH; L_12x12mm_H8mm
R1: 270; R_0805_2012Metric_Pad1.20x1.40mm_HandSolder
U4: AMS1117-3.3; SOT-223-3_TabPin2
U5: LM2596S-5; TO-263-5_TabPin3

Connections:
3V3: C16.1, R1.1, U4.2 (VO); also elsewhere on the board
5V: C19.1, L1.2, U4.3 (VI), U5.4 (FB); also elsewhere on the board
12V: C18.1, U5.1 (VIN); also elsewhere on the board
GND: C16.2, C18.2, C19.2, D1.1 (K), D10.2 (A), U4.1 (GND), U5.3 (GND), U5.5 (~ON~/OFF); also elsewhere on the board
unnamed: D1.2 (A), R1.2
unnamed: D10.1 (K), L1.1, U5.2 (OUT)

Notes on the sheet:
REGULADOR 5V (BUCK)
REGULADOR 3.3V
LED ENCENDIDO

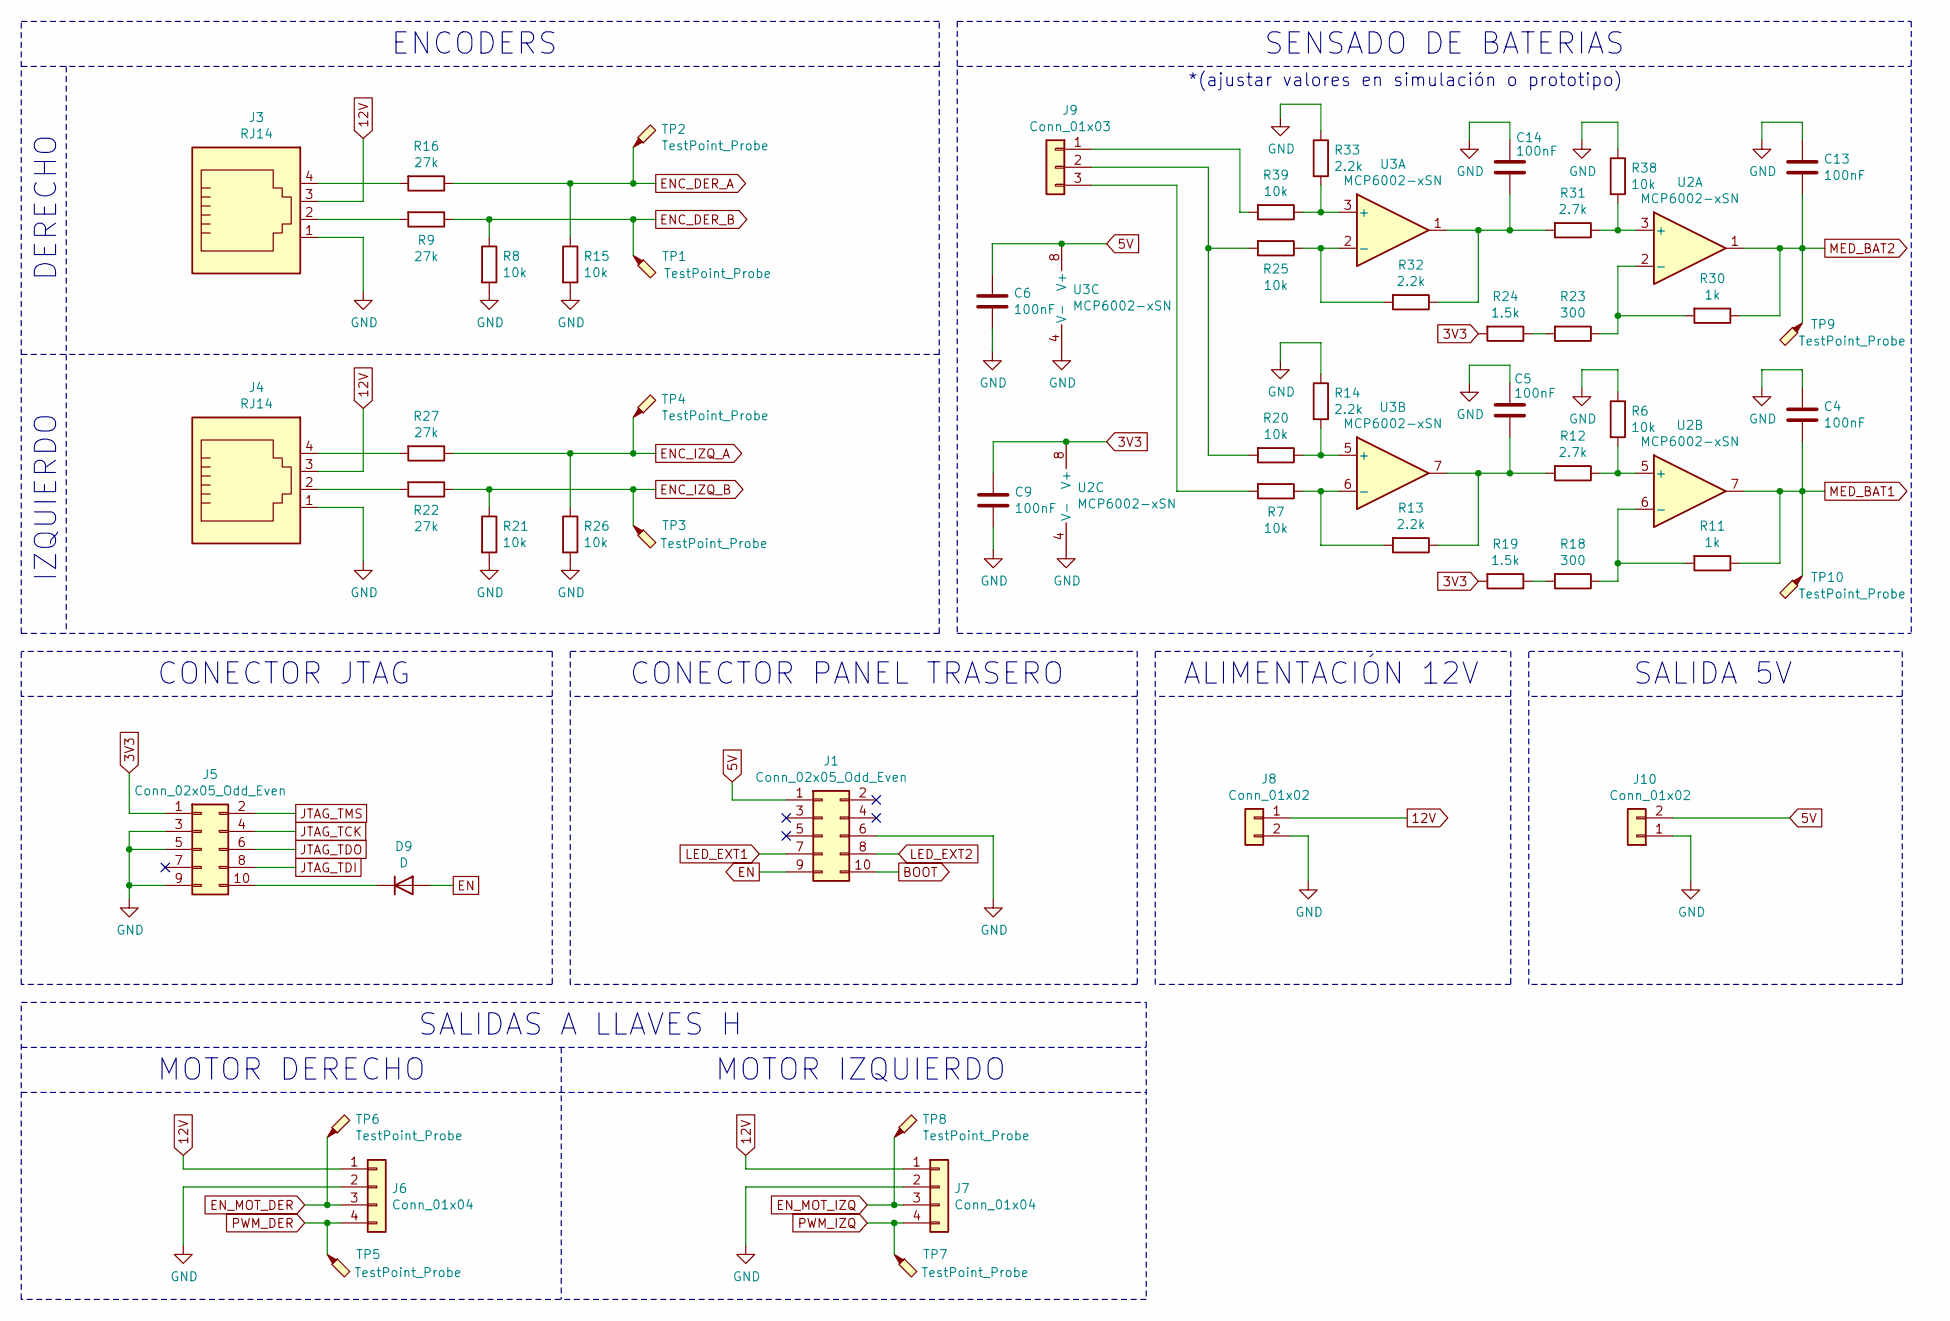
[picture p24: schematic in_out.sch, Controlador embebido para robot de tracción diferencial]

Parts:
C4, C5, C6, C9, C13, C14: 100nF; C_0805_2012Metric_Pad1.18x1.45mm_HandSolder
D9: D; D_SMA
J1: Conn_02x05_Odd_Even; PinHeader_2x05_P2.54mm_Vertical
J3, J4: RJ14; RJ14_Connfly_DS1133-S4_Horizontal
J5: Conn_02x05_Odd_Even; PinHeader_2x05_P1.27mm_Vertical_SMD
J6, J7: Conn_01x04; Molex_KK-254_AE-6410-04A_1x04_P2.54mm_Vertical
J8: Conn_01x02; TerminalBlock_Phoenix_MKDS-1,5-2-5.08_1x02_P5.08mm_Horizont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
J9: Conn_01x03; TerminalBlock_Phoenix_MKDS-1,5-3-5.08_1x03_P5.08mm_Horizont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
J10: Conn_01x02; Molex_KK-254_AE-6410-02A_1x02_P2.54mm_Vertical
R6, R7, R8, R15, R20, R21, R25, R26, R38, R39: 10k; R_0805_2012Metric_Pad1.20x1.40mm_HandSolder
R9, R16, R22, R27: 27k; R_0805_2012Metric_Pad1.20x1.40mm_HandSolder
R11, R30: 1k; R_0805_2012Metric_Pad1.20x1.40mm_HandSolder
R12, R31: 2.7k; R_0805_2012Metric_Pad1.20x1.40mm_HandSolder
R13, R14, R32, R33: 2.2k; R_0805_2012Metric_Pad1.20x1.40mm_HandSolder
R18, R23: 300; R_0805_2012Metric_Pad1.20x1.40mm_HandSolder
R19, R24: 1.5k; R_0805_2012Metric_Pad1.20x1.40mm_HandSolder
TP1, TP2, TP3, TP4, TP5, TP6, TP7, TP8, TP9, TP10: TestPoint_Probe; TestPoint_Pad_1.0x1.0mm
U2, U3: MCP6002-xSN; SOIC-8_3.9x4.9mm_P1.27mm

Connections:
3V3: C9.1, J5.1, R19.2, R24.2, U2.8 (V+); also elsewhere on the board
5V: C6.1, J1.1, J10.2, U3.8 (V+); also elsewhere on the board
12V: J3.3, J4.3, J6.1, J7.1, J8.1; also elsewhere on the board
BOOT: J1.10; also elsewhere on the board
EN: D9.2 (A), J1.9; also elsewhere on the board
ENC_DER_A: R15.1, R16.1, TP2.1; also elsewhere on the board
ENC_DER_B: R8.1, R9.1, TP1.1; also elsewhere on the board
ENC_IZQ_A: R26.1, R27.1, TP4.1; also elsewhere on the board
ENC_IZQ_B: R21.1, R22.1, TP3.1; also elsewhere on the board
EN_MOT_DER: J6.3, TP6.1; also elsewhere on the board
EN_MOT_IZQ: J7.3, TP8.1; also elsewhere on the board
GND: C4.1, C5.1, C6.2, C9.2, C13.1, C14.1, J1.6, J3.1, J4.1, J5.3, J5.5, J5.9, J6.2, J7.2, J8.2, J10.1, R6.1, R8.2, R14.1, R15.2, R21.2, R26.2, R33.1, R38.1, U2.4 (V-), U3.4 (V-); also elsewhere on the board
JTAG_TCK: J5.4; also elsewhere on the board
JTAG_TDI: J5.8; also elsewhere on the board
JTAG_TDO: J5.6; also elsewhere on the board
JTAG_TMS: J5.2; also elsewhere on the board
LED_EXT1: J1.7; also elsewhere on the board
LED_EXT2: J1.8; also elsewhere on the board
MED_BAT1: C4.2, R11.1, TP10.1, U2.7; also elsewhere on the board
MED_BAT2: C13.2, R30.1, TP9.1, U2.1; also elsewhere on the board
unnamed: C5.2, R12.2, R13.1, U3.7
unnamed: C14.2, R31.2, R32.1, U3.1
unnamed: D9.1 (K), J5.10
unnamed: J3.2, R9.2
unnamed: J3.4, R16.2
unnamed: J4.2, R22.2
unnamed: J4.4, R27.2
unnamed: J9.1, R39.2
unnamed: J9.2, R20.2, R25.2
unnamed: J9.3, R7.2
unnamed: R11.2, R18.1, U2.6 (-)
unnamed: R6.2, R12.1, U2.5 (+)
unnamed: R7.1, R13.2, U3.6 (-)
unnamed: R14.2, R20.1, U3.5 (+)
unnamed: R18.2, R19.1
unnamed: R23.1, R30.2, U2.2 (-)
unnamed: R23.2, R24.1
unnamed: R25.1, R32.2, U3.2 (-)
unnamed: R31.1, R38.2, U2.3 (+)
unnamed: R33.2, R39.1, U3.3 (+)
PWM_DER: J6.4, TP5.1; also elsewhere on the board
PWM_IZQ: J7.4, TP7.1; also elsewhere on the board

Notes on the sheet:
ENCODERS
SENSADO DE BATERIAS
IZQUIERDO
DERECHO
CONECTOR JTAG
CONECTOR PANEL TRASERO
ALIMENTACIÓN 12V
SALIDAS A LLAVES H
MOTOR DERECHO
MOTOR IZQUIERDO
*(ajustar valores en simulación o prototipo)
SALIDA 5V

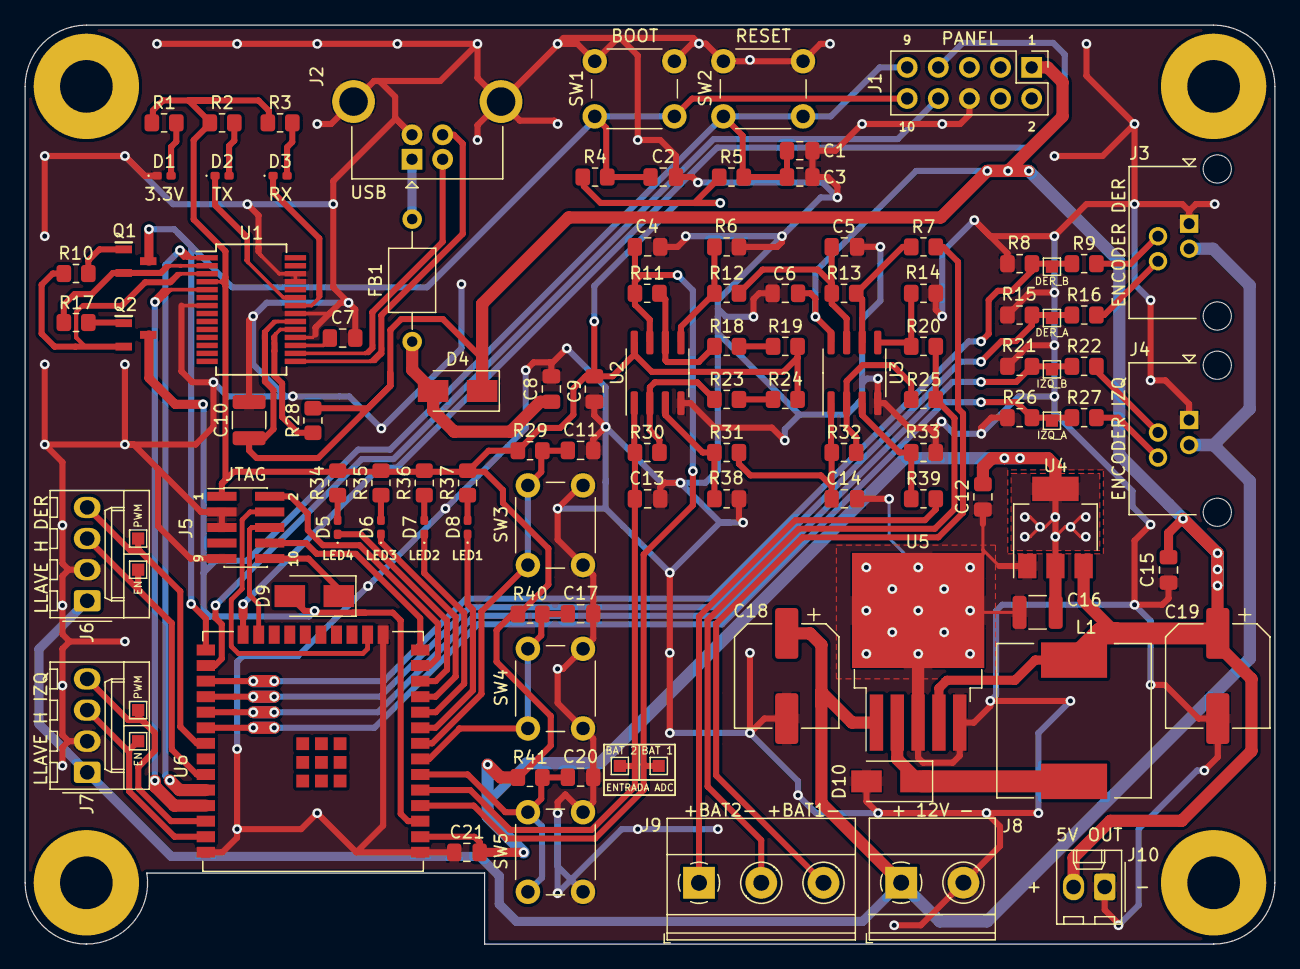
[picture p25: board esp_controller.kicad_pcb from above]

Board: 2 copper layers, 102.0 x 75.0 mm, 111 parts (0 on the bottom side), 71 nets.

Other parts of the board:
H1, H2, H3, H4: MountingHole_4.3mm_M4_Pad

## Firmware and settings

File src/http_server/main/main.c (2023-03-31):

/******************************************************************************
 * Project: DDRC HTTP SERVER
 * File: main.c
 * Description: Main function
 * Created on: 05 jun. 2022
 * Last modified date: 21 Aug. 2022
 * Version: 0.0.1
 *
 * Este archivo complementa el Proyecto Final de grado de:
 * Albarran, Gustavo - Nicolodi, Juan - Ruiz, Dante
 * UNIVERSIDAD TECNOLOGICA NACIONAL - Fac. Reg. Cordoba
 *
 *	NOTE: 
 *  TODO: LEDS, Pulsadores, rango ADC, salidas enable, encoders
 ******************************************************************************/

#include "main.h"

static const char *TAG = "main";

void app_main(void)
{
    /*
        Turn of warnings from HTTP server as redirecting traffic will yield
        lots of invalid requests
    */
    esp_log_level_set("httpd_uri", ESP_LOG_ERROR);
    esp_log_level_set("httpd_txrx", ESP_LOG_ERROR);
    esp_log_level_set("httpd_parse", ESP_LOG_ERROR);
    
    float duty_motor = 50.0;
    pwm_motor_init();
    
    pwm_motor_set_duty(duty_motor,RUEDA_IZQ);
    pwm_motor_set_duty(duty_motor,RUEDA_DER);
    
    // Initialize networking stack
    ESP_ERROR_CHECK(esp_netif_init());

    // Create default event loop needed by the  main app
    ESP_ERROR_CHECK(esp_event_loop_create_default());

    // Initialize NVS needed by Wi-Fi
    ESP_ERROR_CHECK(nvs_flash_init());

    // Initialize Wi-Fi including netif with default config
    esp_netif_create_default_wifi_ap();

    // Initialise ESP32 in SoftAP mode
    wifi_init_softap();

    // Start the server for the first time
    start_webserver();

    // Init GPIO (leds and buttons)
    gpio_init();
    
    // Set initial led status
    led_init();
    
    // Enable buttons interruptions
    buttons_init();
    
    // Set and start ADC for battery meter
    adc_init();
    
    // Set and init Rotary encoder
    encoders_init();
    
    // does nothing loop
    while(1)vTaskDelay(pdMS_TO_TICKS(1000));;
    
}

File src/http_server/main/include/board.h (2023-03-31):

/******************************************************************************
 * Project: DDRC HTTP SERVER
 * File: board.h
 * Description: Board GPIO assigments
 * Created on: 05 jun. 2022
 * Last modified date: 20 Aug. 2022
 * Version: 0.0.1
 *
 * Este archivo complementa el Proyecto Final de grado de:
 * Albarran, Gustavo - Nicolodi, Juan - Ruiz, Dante
 * UNIVERSIDAD TECNOLOGICA NACIONAL - Fac. Reg. Cordoba
 *
 *	NOTE: 
 *
 ******************************************************************************/

#define BOARD DDRC_ESP32

#define BOOT_BUTTON    0

/* Define GPIO */
/* LEDs */
#define LED1    33
#define LED2    25
#define LED3    26
#define LED4    27

/* LEDs Externos */
#define LED_EXT1    2
#define LED_EXT2    4

#define GPIO_OUTPUT_LEDS ((1ULL<<LED1) | (1ULL<<LED2) | (1ULL<<LED3) | (1ULL<<LED4))
#define GPIO_OUTPUT_LEDS_EXT ((1ULL<<LED_EXT1) | (1ULL<<LED_EXT2) ) 
#define GPIO_OUTPUT_PIN_SEL  (GPIO_OUTPUT_LEDS | GPIO_OUTPUT_LEDS_EXT)

/* PULSADORES */
#define PUL1    34
#define PUL2    35
#define PUL3    32

#define GPIO_INPUT_PIN_SEL  ((1ULL<<PUL1) | (1ULL<<PUL2) | (1ULL<<PUL3))


/* ENCODERS */
#define ENC_IZQ_A   18
#define ENC_IZQ_B   5
#define ENC_DER_A   17
#define ENC_DER_B   16

/* PWM MOTORES */
#define PWM_IZQ     22
#define PWM_DER     19

/* Habilitacion MOTORES */
#define EN_MOT_IZQ  23
#define EN_MOT_DER  21

#define ENABLE_MOTOR_MASK  ((1ULL<<EN_MOT_IZQ) | (1ULL<<EN_MOT_DER))

/* Ruedas */
#define RUEDA_IZQ      0
#define RUEDA_DER      1

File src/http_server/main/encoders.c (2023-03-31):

/******************************************************************************
 * Project: DDRC HTTP SERVER
 * File: encoders.c
 * Description: Functions for read and parce the wheel's encoders
 * Created on: 12 jun. 2022
 * Last modified date: 12 jun. 2022
 * Version: 0.0.1
 *
 * Este archivo complementa el Proyecto Final de grado de:
 * Albarran, Gustavo - Nicolodi, Juan - Ruiz, Dante
 * UNIVERSIDAD TECNOLOGICA NACIONAL - Fac. Reg. Cordoba
 *
 *	NOTE: 
 *
 ******************************************************************************/

#include "encoders.h"
static const char *TAG = "encoders";

static TaskHandle_t handler_task_encoders_vel = NULL;
static rotary_encoder_t *encoder1 = NULL;
static rotary_encoder_t *encoder2 = NULL;


float enc1_vel = 0; // Encoders measure velocity
float enc2_vel = 0;


/**
* @brief   Task for calculate angular velocity
*
* @param   - void
*
* @return  - void
* 
*/
void task_encoders_vel(void *arg){
    
    // init and finish encoders values
    float pos_enc1_1, pos_enc1_2;
    float pos_enc2_1, pos_enc2_2;
    // delta of time, milisec
    int delta_time = 100;
    
    while(1){
        // read init positions
        pos_enc1_1 = encoder1->get_counter_value(encoder1);
        pos_enc2_1 = encoder2->get_counter_value(encoder2);
        
        vTaskDelay(pdMS_TO_TICKS(delta_time)); // wait 100 ms
        
        // read finish positions
        pos_enc1_2 = encoder1->get_counter_value(encoder1);
        pos_enc2_2 = encoder2->get_counter_value(encoder2);
        
        // reset positions to prevent overflow
        // encoder1->del(encoder1);
        // encoder2->del(encoder2);
        // Parse to rad/seg
        enc1_vel = 2*3.14*(pos_enc1_2-pos_enc1_1)/(ENCODER1_STEPS*delta_time*0.001);
        enc2_vel = 2*3.14*(pos_enc2_2-pos_enc2_1)/(ENCODER2_STEPS*delta_time*0.001);
        
        
    }
}


/**
* @brief    Init the encoders
*
* @param   	- void
*
* @return  
*          - void
*/
void encoders_init(void){
    // Rotary encoder underlying device is represented by a PCNT unit in this example
    uint32_t pcnt_unit1 = 0;
    uint32_t pcnt_unit2 = 1;

    // Create rotary encoder1 instance
    rotary_encoder_config_t config1 = ROTARY_ENCODER_DEFAULT_CONFIG((rotary_encoder_dev_t)pcnt_unit1, ENC_DER_A, ENC_DER_B);
    ESP_ERROR_CHECK(rotary_encoder_new_ec11(&config1, &encoder1));
    // Filter out glitch (1us)
    ESP_ERROR_CHECK(encoder1->set_glitch_filter(encoder1, 1));
    

    // Create rotary encoder2 instance
    rotary_encoder_config_t config2 = ROTARY_ENCODER_DEFAULT_CONFIG((rotary_encoder_dev_t)pcnt_unit2, ENC_IZQ_A, ENC_IZQ_B);
    ESP_ERROR_CHECK(rotary_encoder_new_ec11(&config2, &encoder2));
    // Filter out glitch (1us)
    ESP_ERROR_CHECK(encoder2->set_glitch_filter(encoder2, 1));

    // Start encoders
    ESP_ERROR_CHECK(encoder1->start(encoder1));
    ESP_ERROR_CHECK(encoder2->start(encoder2));



    // Task for update encoders angular velocity
    xTaskCreate(task_encoders_vel, "task_encoders_vel", 
        TASK_ENCODERS_VEL_STACK_SIZE, NULL, 16, &handler_task_encoders_vel);


    // Report counter value
    while (1) {
                        
        ESP_LOGI(TAG, "|Encoder 1: %f  | Encoder 2: %f|", enc1_vel,enc2_vel);
        vTaskDelay(pdMS_TO_TICKS(1000));
    }
}

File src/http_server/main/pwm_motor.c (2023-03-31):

/******************************************************************************
 * Project: DDRC HTTP SERVER
 * File: pwm_motor.c
 * Description: Functions for PWM motor control driver
 * Created on: 05 jun. 2022
 * Last modified date: 21 Aug. 2022
 * Version: 0.0.1
 *
 * Este archivo complementa el Proyecto Final de grado de:
 * Albarran, Gustavo - Nicolodi, Juan - Ruiz, Dante
 * UNIVERSIDAD TECNOLOGICA NACIONAL - Fac. Reg. Cordoba
 *
 *	NOTE: 
 *
 ******************************************************************************/

#include "driver/gpio.h"
#include "pwm_motor.h"
static const char *TAG = "pwm_motor";


/**
* @brief    Set the duty cycle of Left or Rigth motors
*
* @param   	- duty_cycle : float from 0 to 100. 0 to max reverse, 50 for stop, 
*                           100 for max to direct velocity
*           - wheel :   RUEDA_IZQ or RUEDA_DER
*
* @return  
*          - void
*/
void pwm_motor_set_duty(float duty_cycle, int wheel)
{
    /* motor moves with duty cycle = duty % */
    if ((duty_cycle >= 0) && (duty_cycle <= 100)) {
        if(wheel == RUEDA_IZQ){
            //mcpwm_set_signal_low(BDC_MCPWM_UNIT, BDC_MCPWM_TIMER, MCPWM_OPR_A);
            mcpwm_set_duty(BDC_MCPWM_UNIT, BDC_MCPWM_TIMER, MCPWM_OPR_A, duty_cycle);
            mcpwm_set_duty_type(BDC_MCPWM_UNIT, BDC_MCPWM_TIMER, MCPWM_OPR_A, MCPWM_DUTY_MODE_0);
            ESP_LOGI(TAG, "IZQ = %.2f Duty",duty_cycle);
        }
        if(wheel == RUEDA_DER){
            //mcpwm_set_signal_low(BDC_MCPWM_UNIT, BDC_MCPWM_TIMER, MCPWM_OPR_A);
            mcpwm_set_duty(BDC_MCPWM_UNIT, BDC_MCPWM_TIMER, MCPWM_OPR_B, duty_cycle);
            mcpwm_set_duty_type(BDC_MCPWM_UNIT, BDC_MCPWM_TIMER, MCPWM_OPR_B, MCPWM_DUTY_MODE_0);
            ESP_LOGI(TAG, "DER = %.2f Duty",duty_cycle);
        }
    }
}


/**
* @brief    Enable motor drivers
*
* @param   	- void
*
* @return  
*           - void
*/
void pwm_motor_enable( void ){
    gpio_set_level(EN_MOT_IZQ, 0);
    gpio_set_level(EN_MOT_DER, 0);
}


/**
* @brief    Disable motor drivers
*
* @param   	- void
*
* @return  
*           - void
*/
void pwm_motor_stop( void ){
    gpio_set_level(EN_MOT_IZQ, 1);
    gpio_set_level(EN_MOT_DER, 1);
    pwm_motor_set_duty(50, RUEDA_IZQ);
    pwm_motor_set_duty(50, RUEDA_DER);
    
}


/**
* @brief    Move forward, with a fixed 75% Duty Cycle
*
* @param   	- void
*
* @return  
*          - void
*/
void pwm_motor_move_forward( void ){
       float duty_forward = 25.0;
       pwm_motor_move(duty_forward, duty_forward);
}


/**
* @brief    Move back, with a fixed 25% Duty Cycle
*
* @param   	- void
*
* @return  
*          - void
*/
void pwm_motor_move_back( void ){
       float duty_back= 75.0;
       pwm_motor_move(duty_back, duty_back);
}

/**
* @brief    Rotate to the left
*
* @param   	- void
*
* @return  
*          - void
*/
void pwm_motor_rotate_left( void ){
       float duty_left = 25.0;
       float duty_right = 75.0;
       pwm_motor_move(duty_left, duty_right);
}


/**
* @brief    Rotate to the right
*
* @param   	- void
*
* @return  
*          - void
*/
void pwm_motor_rotate_right( void ){
       float duty_left = 75.0;
       float duty_right = 25.0;
       pwm_motor_move(duty_left, duty_right);
}


/**
* @brief    Move motors with fixed duty cycles for ever wheel
*
* @param   	- void
*
* @return  
*          - void
*/
void pwm_motor_move(float duty_left, float duty_right){
       pwm_motor_stop();
       pwm_motor_set_duty(duty_left, RUEDA_IZQ);
       pwm_motor_set_duty(duty_right, RUEDA_DER);
       pwm_motor_enable();
}


/**
* @brief    init the PWM unit
*
* @param   	- void
*           
* @return  
*          - void
*/
void pwm_motor_init(void)
{
    // GPIO config on gpio_conf.c

    // MOTOR IZQ
    ESP_LOGI(TAG, "configure mcpwm Left gpio A\n");
    mcpwm_gpio_init(BDC_MCPWM_UNIT, MCPWM0A, BDC_MCPWM_GENA_GPIO_NUM);
    // MOTOR DER
    ESP_LOGI(TAG, "configure mcpwm Right gpio B\n");
    mcpwm_gpio_init(BDC_MCPWM_UNIT, MCPWM0B, BDC_MCPWM_GENB_GPIO_NUM);
    ESP_LOGI(TAG, "init mcpwm driver\n");
    
    
    // MCPWM config struct
    mcpwm_config_t pwm_config = {
        .frequency = BDC_MCPWM_FREQ_HZ,
        .cmpr_a = 0,
        .cmpr_b = 0,
        .counter_mode = MCPWM_UP_COUNTER,
        .duty_mode = MCPWM_DUTY_MODE_0, // Active high duty
    };
    ESP_ERROR_CHECK(mcpwm_init(BDC_MCPWM_UNIT, BDC_MCPWM_TIMER, &pwm_config));

    ESP_LOGI(TAG, "init motor control timer\r\n");
    gptimer_handle_t gptimer;
    gptimer_config_t timer_config = {
        .clk_src = GPTIMER_CLK_SRC_APB,
        .direction = GPTIMER_COUNT_UP,
        .resolution_hz = 1000000, // 1MHz, 1 tick = 1us
    };
    ESP_ERROR_CHECK(gptimer_new_timer(&timer_config, &gptimer));
    pwm_motor_stop();
}

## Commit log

2023-03-17 Add .gitignore for kicad files
2023-03-17 Add kicad files of ddrc-esp32 board
    [esp_controller-B_Cu.gbr, esp_controller-B_Mask.gbr, esp_controller-B_Paste.gbr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]
2023-03-17 Add kicad_lib folder and moves files
    [AMS1117-3.3.stp, BAT760-7.stl, BAT760-7.stp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]
